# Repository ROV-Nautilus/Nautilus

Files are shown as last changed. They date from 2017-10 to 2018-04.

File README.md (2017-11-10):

# Nautilus
Les fonds marins réunissent aujourd'hui de nombreux secteurs et enjeux, tant professionels que particuliers. On y retrouve entre autre l'exploration sous-marine, la surveillance et maintenance d'installations professionelles, ainsi que la cartographie des fonds marins. Tout ces domaines demandent le développement de solutions techniques plus rentables et pratiques qu'une intervention humaine. Notre projet propose ainsi un ROV (Remotely Operated Vehicle) polyvalent et simple d'utilisation à cet effet.

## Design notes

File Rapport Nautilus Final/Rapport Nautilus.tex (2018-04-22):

\documentclass[a4paper,11pt]{report}
 
% Import des extensions
\usepackage[T1]{fontenc}
\usepackage[utf8]{inputenc}
\usepackage[francais]{babel}
\usepackage{graphicx}
\usepackage{color}
\usepackage[table]{xcolor}
\usepackage{colortbl}
\usepackage{geometry}
\usepackage{caption}
\usepackage{subcaption}
\usepackage{hyperref}
\usepackage{fullpage}
\usepackage{listings}
\usepackage{lipsum}
\usepackage{eso-pic}
\usepackage[nottoc]{tocbibind}
\geometry{hmargin=2.5cm,vmargin=3.5cm}

\definecolor{darkWhite}{rgb}{0.94,0.94,0.94}

\lstset{
  aboveskip=3mm,
  belowskip=-2mm,
  backgroundcolor=\color{darkWhite},
  basicstyle=\footnotesize,
  breakatwhitespace=false,
  breaklines=true,
  captionpos=b,
  commentstyle=\color{red},
  deletekeywords={...},
  escapeinside={\%*}{*)},
  extendedchars=true,
  framexleftmargin=16pt,
  framextopmargin=3pt,
  framexbottommargin=6pt,
  frame=tb,
  keepspaces=true,
  keywordstyle=\color{purple},
  literate=
  {²}{{\textsuperscript{2}}}1
  {⁴}{{\textsuperscript{4}}}1
  {⁶}{{\textsuperscript{6}}}1
  {⁸}{{\textsuperscript{8}}}1
  {€}{{\euro{}}}1
  {é}{{\'e}}1
  {è}{{\`{e}}}1
  {ê}{{\^{e}}}1
  {ë}{{\¨{e}}}1
  {É}{{\'{E}}}1
  {Ê}{{\^{E}}}1
  {û}{{\^{u}}}1
  {ù}{{\`{u}}}1
  {â}{{\^{a}}}1
  {à}{{\`{a}}}1
  {á}{{\'{a}}}1
  {ã}{{\~{a}}}1
  {Á}{{\'{A}}}1
  {Â}{{\^{A}}}1
  {Ã}{{\~{A}}}1
  {ç}{{\c{c}}}1
  {Ç}{{\c{C}}}1
  {õ}{{\~{o}}}1
  {ó}{{\'{o}}}1
  {ô}{{\^{o}}}1
  {Õ}{{\~{O}}}1
  {Ó}{{\'{O}}}1
  {Ô}{{\^{O}}}1
  {î}{{\^{i}}}1
  {Î}{{\^{I}}}1
  {í}{{\'{i}}}1
  {Í}{{\~{Í}}}1,
  morekeywords={*,...},
  numbers=left,
  numbersep=10pt,
  numberstyle=\tiny\color{black},
  rulecolor=\color{black},
  showspaces=false,
  showstringspaces=false,
  showtabs=false,
  stepnumber=1,
  stringstyle=\color{gray},
  tabsize=4,
  title=\lstname,
}

\newcommand{\blap}[1]{\vbox to 0pt{#1\vss}}
\newcommand\AtUpperLeftCorner[3]{%
\put(\LenToUnit{#1},\LenToUnit{\dimexpr\paperheight-#2}){\blap{#3}}%
}
\newcommand\AtTopCenterPage[2]{%
\put(\LenToUnit{.5\paperwidth},\LenToUnit{\dimexpr\paperheight-#1}){\blap{\hbox to 0pt{\hss#2\hss}}}%
}
\newcommand\AtUpperRightCorner[3]{%
\put(\LenToUnit{\dimexpr\paperwidth-#1},\LenToUnit{\dimexpr\paperheight-#2}){\blap{\llap{#3}}}%
}

\author{Dylan Bideau, Julien Turpin, Pierre Bogrand, Guillaume Vincenti}
\title{\huge{Nautilus - Rapport}}
\date{22 Avril 2018}

\begin{document}
\makeatletter
\begin{titlepage}

	\AddToShipoutPicture{
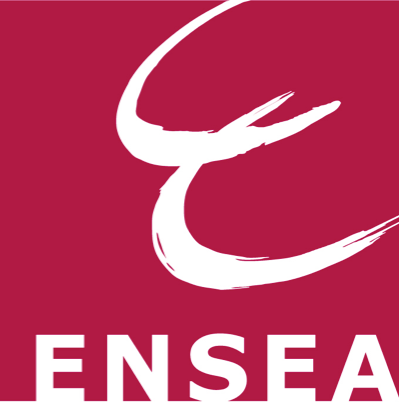
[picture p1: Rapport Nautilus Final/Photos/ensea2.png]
		\AtUpperLeftCorner{1.5cm}{1cm}{}
	}
	\AddToShipoutPicture{
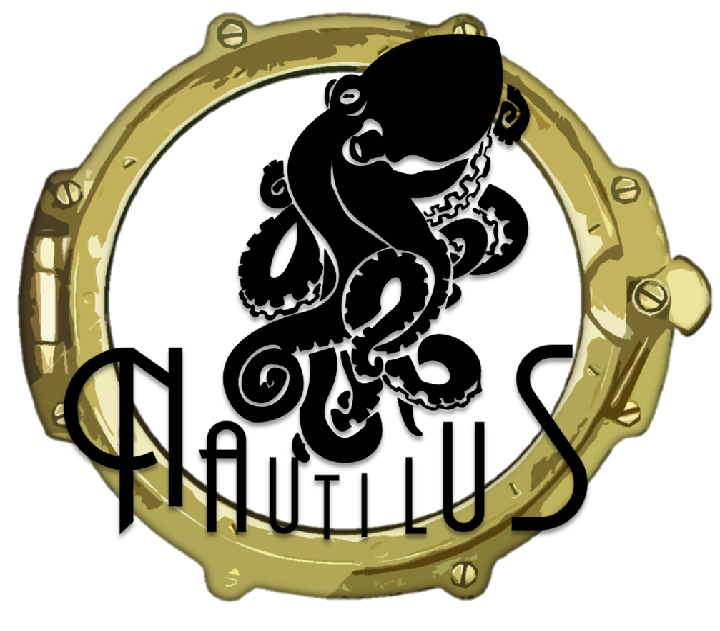
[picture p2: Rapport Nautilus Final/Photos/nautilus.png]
		\AtUpperRightCorner{1.5cm}{1cm}{}
	}

	\begin{center}
		\vspace*{10cm}
		\textsc{\@title}
		\vspace*{0.5cm}
		\hrule
		\vspace*{0.5cm}
		\large{\@author}
	\end{center}
	\vspace*{9.2cm}
	\begin{center}
		\large{\@date}
	\end{center}
\end{titlepage}
\ClearShipoutPicture

\renewcommand{\contentsname}{Sommaire}
\tableofcontents

\chapter{Introduction}

        Les fonds marins réunissent aujourd'hui de nombreux secteurs et enjeux, tant professionnels que particuliers. On y retrouve entre autre l'exploration sous-marine, la surveillance et maintenance d'installations professionnelles, ainsi que la cartographie des fonds marins. Tout ces domaines demandent le développement de solutions techniques plus rentables et pratiques qu'une intervention humaine. Notre projet propose ainsi un ROV (Remotely Operated Vehicle) polyvalent et simple d'utilisation à cet effet.

\chapter{Présentation du projet}
        
				Un ROV est un robot sous-marin contrôlé à distance et permettant une acquisition d'informations, visuelles ou à partir de capteurs. Notre projet de ROV filoguidé, Nautilus, sera transportable et pilotable à l'aide d'un ordinateur portable. Il permettra d'observer facilement des installations ou des fonds marins à l'aide de caméras. Disposant également de fonctions avancées, le Nautilus sera en mesure de recréer le fond marin d'une zone géographique déterminée par l'utilisateur à partir d'une batterie de photographies prises lors de la phase d'exploration. Les différentes fonctionnalités du Nautilus en font ainsi un outil polyvalent, permettant exploration, maintenance et cartographie des fonds.

\chapter{Cahier des charges}

        \section{Analyse Fonctionnelle}
						\subsection{Structure}
								Facilement transportable et peu encombrant.\newline
								\textbf{Contraintes :}
								\begin{itemize}
										\item Poids : 2-3kg
										\item Dimension : 300*200*150mm
										\item Étanche de norme IP 68 \newline \newline
									\end{itemize}

						\subsection{Commandabilité}
								Commandé à distance par une liaison filaire.\newline
								\textbf{Contraintes :}
								\begin{itemize}
										\item Câble : 15m
										\item Carte intégrée dans le ROV
										\item FPV (First Person View)
										\item Piloté au clavier\newline \newline
								\end{itemize}

						\subsection{Milieu d'utilisation}
								Adapté aux contraintes imposées par son environnement. \newline
								\textbf{Contraintes :}
								\begin{itemize}
										\item Eau non salé (moins de 1 g de sels dissous par kilogramme d'eau)
										\item Eau translucide (transmittance de la lumière entre 75\% et 95\%)
										\item Lieu : Piscine, lac
										\item Écoulement laminaire
										\item Courant marin inférieur à 2 nœuds
										\item Profondeur de 10m (résistant à 2 bars) \newline \newline
								\end{itemize}

						\subsection{Énergie}
								Être entièrement autonome. \newline
								\textbf{Contraintes :}
								\begin{itemize}
										\item Autonomie de 20 minutes
								\end{itemize}

						\subsection{Motorisation}
								Être mobile une fois immergé. \newline
								\textbf{Contraintes :}
								\begin{itemize}
										\item Propulsion électrique
										\item Déplacement horizontal (Vitesse maximale de 1m/s)
										\item Déplacement vertical (Vitesse maximale de 0.5m/s)
										\item Direction droite/gauche à 360 degrés   \newline \newline
								\end{itemize}

						\subsection{Acquisitions}
								Acquérir et transmettre l'information. \newline
								\textbf{Contraintes :}
								\begin{itemize}
										\item Acquisition et retransmission d'un signal vidéo
										\item Acquisition et stockage de photographies
										\item Mesure de la pression
										\item Mesure de la position relative avec signaux GPS
								\end{itemize}

\chapter{Outils de gestion}

        \section{Trello}
					Notre premier outil de gestion est Trello. Il nous permet de gérer notre projet en terme de planification des tâches. Nous utilisons un code couleur pour chaque membre du projet :
						\begin{figure}[!h]
							\begin{center}
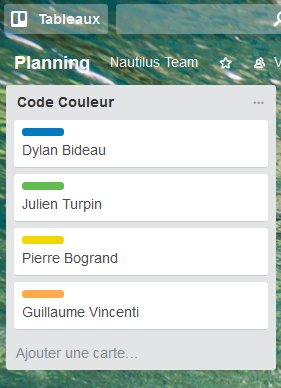
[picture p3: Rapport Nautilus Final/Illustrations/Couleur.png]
								
								\caption{Trello - Code Couleur}
							\end{center}
						\end{figure}
						\newline Voici actuellement ce que nous devons faire (Lors du premier livrable) :
						\begin{figure}[!h]
							\begin{center}
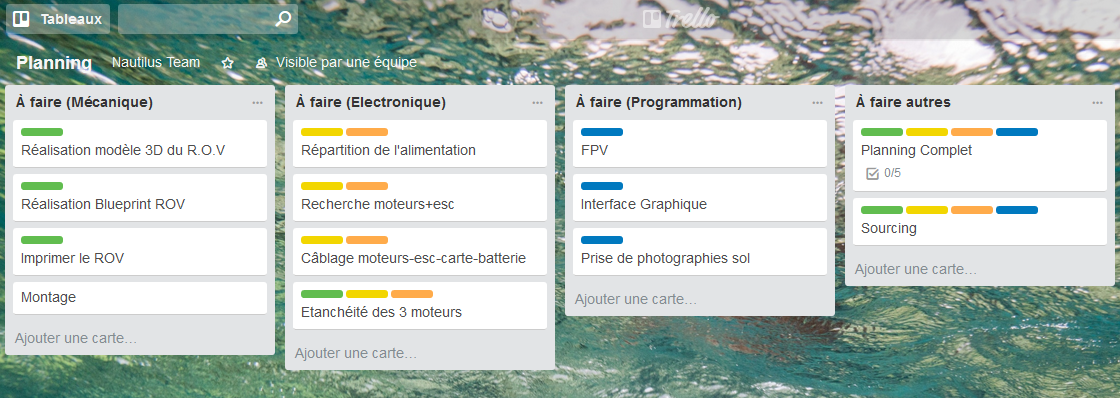
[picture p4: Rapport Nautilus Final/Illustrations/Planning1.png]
								
								\caption{Trello - Planning A faire}
							\end{center}
						\end{figure}
						\newpage Et ce que nous sommes en train de faire ainsi que les tâches terminées :
						\begin{figure}[!h]
							\begin{center}
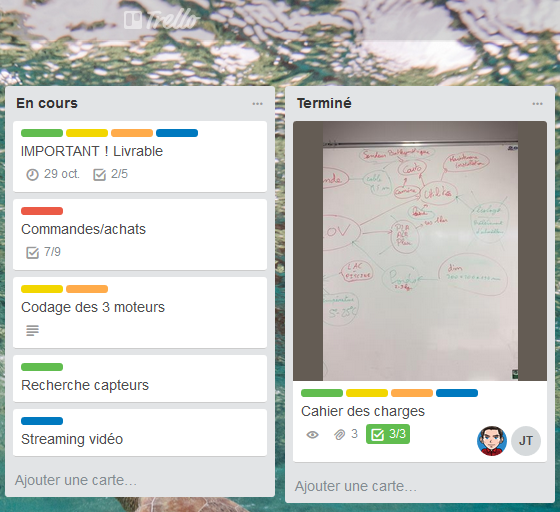
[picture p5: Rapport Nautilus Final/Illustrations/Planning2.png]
								
								\caption{Trello - Planning En cours et Terminé}
							\end{center}
						\end{figure}
						
        \section{Github}
				Tout notre code, que cela soit pour les documents en latex ou les codes liés au projet, est sur Github :
				\url{https://github.com/ROV-Nautilus/Nautilus}.
				\newline En voici un aperçu :
					\begin{figure}[!h]
							\begin{center}
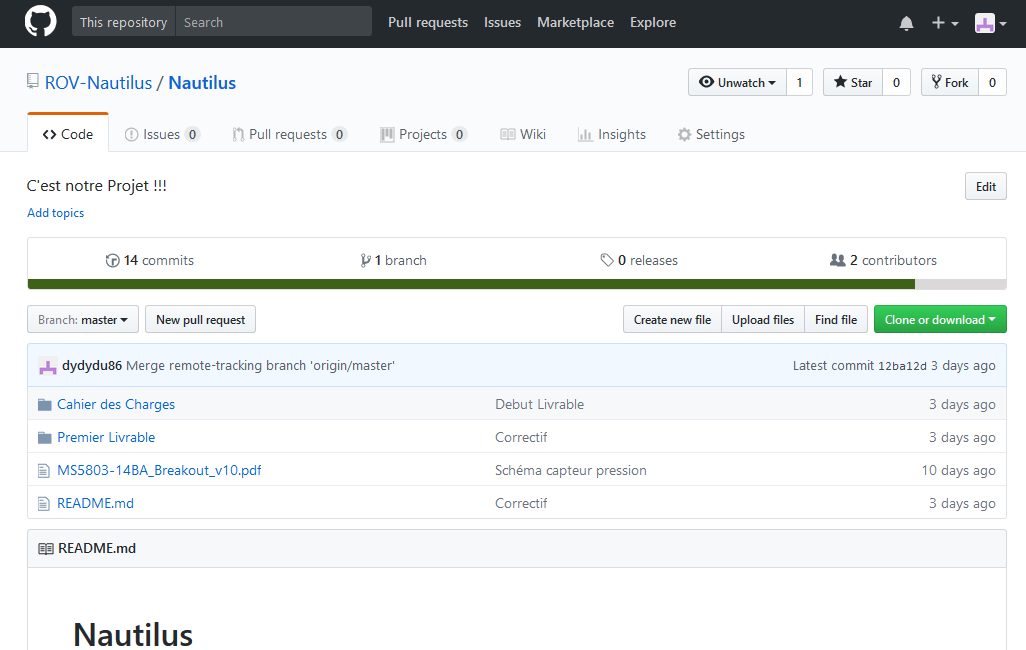
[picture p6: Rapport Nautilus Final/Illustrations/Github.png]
								
								\caption{Github - Nautilus}
							\end{center}
						\end{figure}
				
				\section{Gestion de Budget}
				La gestion de notre budget est réalisé à l'aide d'Excel et de Trello, en effet Trello nous permet de mettre en commun les propositions de dépenses et avec Excel nous stockons l'ensemble des commandes par fournisseurs. \newline \newline Les voici ci-dessous :
					\begin{figure}[!h]
							\begin{center}
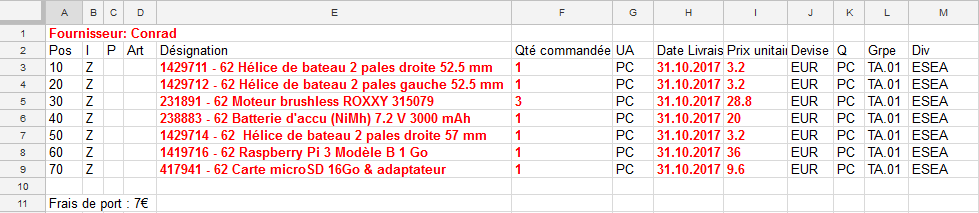
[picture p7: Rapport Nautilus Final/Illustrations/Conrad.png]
								
								\caption{Commande Conrad}
							\end{center}
					\end{figure}
					\begin{figure}[!h]
							\begin{center}
								
								\caption{Commande Robotshop}
							\end{center}
					\end{figure}
					\begin{figure}[!h]
							\begin{center}
								
								\caption{Commande ExpTech}
							\end{center}
					\end{figure}
								
\chapter{Motorisation et énergie}

				\section{Moteurs brushless et ESC} 
				
							Dans un premier temps, il a été question de la technologie des moteurs à utiliser. Après une étude des différentes solutions disponibles, nous avons finalement choisi des moteurs brushless \cite{ref5}. En effet, les moteurs brushless sont des machines synchrones auto-pilotées à aimants permanents et donc sans balais.
			\begin{figure}[!h]
				\begin{center}
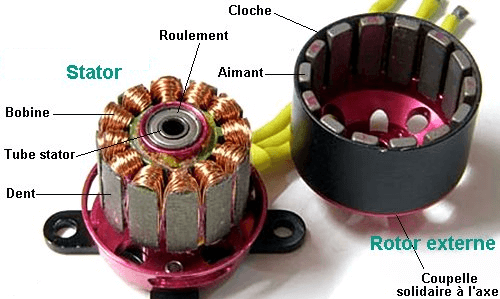
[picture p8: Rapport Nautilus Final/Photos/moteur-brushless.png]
					
					\caption{Moteur Brushless}
				\end{center}
			\end{figure}\newline
							Le principal avantage de ces moteurs est qu'ils peuvent être utilisés immergés dans l'eau sans aucun traitement particulier au préalable. En revanche, un système électronique de commande doit assurer la commutation du courant dans les enroulements statoriques : les ESC, ou Electronic Speed Controllers.
			Un ESC transforme un signal d'alimentation continu, dans notre cas issu d'une batterie, en un signal triphasé envoyé ensuite au moteur brushless. Pour contrôler la vitesse de rotation du moteur, on envoie à l'ESC un signal de commande, généralement créneau, et dont le rapport cyclique définit la vitesse du moteur. 
			\begin{figure}[!h]
				\begin{center}
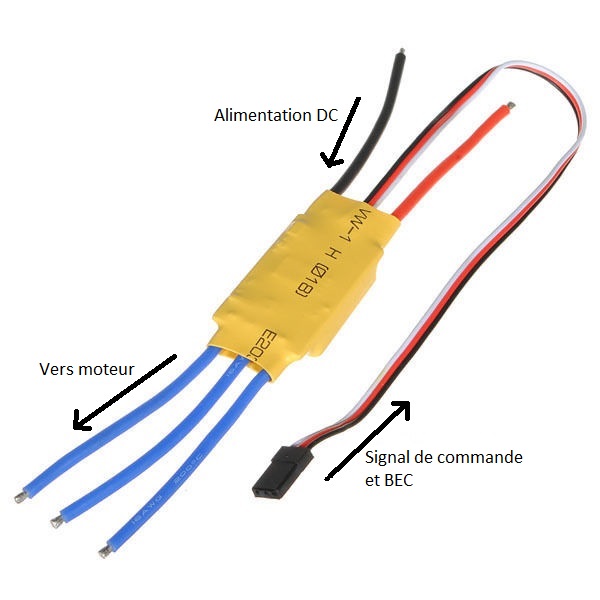
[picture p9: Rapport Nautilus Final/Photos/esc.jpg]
					
					\caption{ESC}
				\end{center}
			\end{figure}
			\newpage 
			Les trois ESC utilisés dans un premier temps pour nos moteurs \cite{ref6} sont également équipés d'un circuit éliminateur de batterie, ou BEC, permettant de générer un signal d'alimentation constant de 5V et 3A maximum. Ce dernier permet d'alimenter un autre composant, comme une carte Raspberry Pi dans notre cas, sans avoir à recourir à une seconde batterie. 
			\newline\newline Cependant, ces ESC ne permettent la rotation du moteur que dans un seul sens. Le seul moyen de modifier le sens de rotation du moteur dans ce cas est d'échanger deux des trois signaux déphasés envoyés au moteur. La direction droite/gauche étant assurée par les deux moteurs de propulsion arrière, cette particularité n'est pas problématique: la rotation plus rapide d'un des deux moteurs arrière par rapport à l'autre permet de diriger le ROV à gauche ou à droite. En revanche, le moteur vertical devant assuré la propulsion verticale doit pouvoir tourner dans les deux sens. Un second modèle d'ESC a donc été nécessaire pour permettre au moteur de tourner dans les deux sens. Ce dernier \cite{ref7} possède ainsi un mode "reverse" permettant au moteur de tourner dans les deux sens, ainsi qu'un BEC, et sera donc attribué au moteur vertical du ROV.
	
				\newpage\section{Calibration et commande des ESC}
				
				Traditionnellement, le signal de contrôle envoyé à l'ESC est un signal PWM de fréquence 50 Hz environ, un certain écart de cette valeur étant accepté. Dans notre cas, le signal est généré par une Raspberry Pi 3, et l'amplitude du signal est donc de 3,3 V environ.
				\begin{figure}[!h]
				  \begin{center}
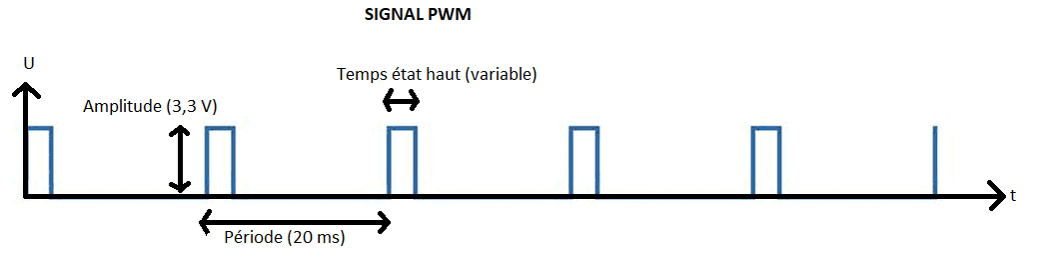
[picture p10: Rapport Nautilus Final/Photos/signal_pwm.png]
				  	
						\caption{Signal PWM}
				  \end{center}
		  	\end{figure}
				\newline\newline La caractéristique la plus importante de ce signal est la largeur de chaque impulsion. C'est cette dernière, généralement entre 0.5 ms et 2.5 ms, qui commande directement l'amplitude du signal envoyé aux moteurs et donc leur vitesse de rotation. Notre carte doit donc être capable de générer un signal créneau à 50 Hz, et de rapport cyclique variable sur commande. Pour générer un tel signal, on utilise le programme \cite{ref8}, disponible sur Github. En effet ce dernier a été conçu pour piloter des servomoteurs à partir des pins GPIO de la Raspberry Pi, et est donc le plus adapté pour générer un tel signal. Pour installer ServoBlaster sur la carte, on rentre les commandes suivantes sur le terminal de Raspbian:
				\begin{figure}[!h]
				  \begin{center}
				  	
						\caption{Programme Servoblaster}
				  \end{center}
		  	\end{figure}
				
				Une fois cette installation effectuée, on peut générer le signal à l'aide de la commande, toujours dans le terminal de Raspbian, "echo x=y > /dev/servoblaster", où x représente le GPIO que l'on utilise et y la valeur du temps d'état haut, en dizaine de us ( par exemple y=100 correspond à un temps d'état haut de 1 ms). Les valeurs de y peuvent aller de 50 à 250, correspondant respectivement à un temps haut de 0.5 ms et 2.5 ms. \newpage Les valeurs de x désignent les GPIO suivant:
					\begin{figure}[!h]
				  \begin{center}
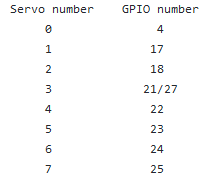
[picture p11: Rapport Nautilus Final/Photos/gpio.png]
				  	
						\caption{Valeurs GPIO}
				  \end{center}
		  	\end{figure}
				
				On obtient ainsi des commandes comme ci-dessous:
				
					\begin{figure}[!h]
				  \begin{center}
				  	
						\caption{Commandes moteurs}
				  \end{center}
		  	\end{figure}
			
			Avec chaque nouvelle valeur de y modifiant la valeur du temps haut du signal sortant. \newline
			
			Toutefois, avant leur utilisation, les ESC nécessitent d'être calibrés. En effet, en fonction des radiocommandes ou autre dispositifs de commande utilisés, l'intervalle des valeurs du temps d'état haut du signal de commande envoyé à l'ESC peux différer. L'ESC doit donc être calibré pour que la valeur maximale de temps d'état haut corresponde à la vitesse maximale de rotation du moteur. De même pour une valeur neutre (moteur à l'arrêt), et une valeur minimale correspondant à la vitesse de rotation inverse maximale, disponible uniquement pour l'ESC "Reverse"', et donc le moteur vertical associé. \newline
			La calibration ne peut pas être effectuée à l'aide des commandes issues de ServoBlaster, l'ESC nécessitant une variation douce du temps d'état haut pour cela. C'est le cas d'un joystick de télécommande, mais pas du programme ne permettant que des variations abrupts de la valeur du temps d'état haut. La calibration des ESC a donc été effectuée à l'aide d'une radiocommande disponible à l'ENSEA \cite{ref9}. Pour cela, on place le joystick de la manette au point neutre, on branche l'ESC à l'émetteur de la radiocommande et on allume dans l'ordre la radiocommande, puis l'ESC. Lorsque ce dernier s'allume, il associe ainsi automatiquement le signal en train d'être reçu au point neutre, donc moteur immobile. On effectue la même opération avec le joystick au maximum pour calibrer la valeur maximale de temps d'état haut et l'associer à la vitesse maximale de rotation du moteur. Une fois cette calibration effectuée, l'ESC en marche ne fonctionnera qu'après avoir reçu le signal correspondant à l'état neutre pendant un certain temps. Cela permet d'éviter entre autres un démarrage intempestif des moteurs. \newline
			
			Une fois la calibration effectuée, on observe à l'oscilloscope le signal de commande envoyé par la manette pour déterminer le temps d'état haut correspondant au point neutre, à la vitesse maximale, et à la vitesse maximale en rotation inverse pour le moteur vertical.
\newline On obtient les résultats suivants:
			
			\begin{figure}[!h]
				  \begin{center}
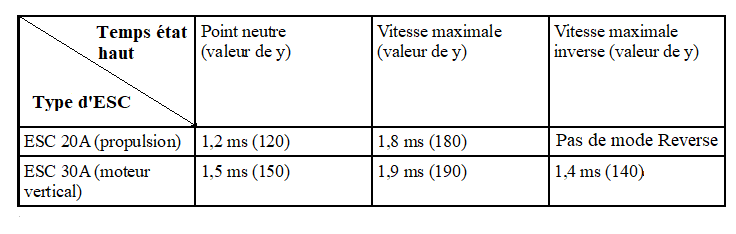
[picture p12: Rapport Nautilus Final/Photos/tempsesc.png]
				  	
						\caption{Tableau des temps}
				  \end{center}
		  	\end{figure}
				
				Après calibration et relevé de ces valeurs, on peut bien commander les 3 moteurs à l'aide des commandes de ServoBlaster. \newpage
				
				\section{Alimentation et montage}
				
				On utilise pour l'alimentation des ESC et des moteurs une batterie NiMh, de capacité 3000 mAh et délivrant une tension de 7,2 V \cite{ref10}. L'alimentation de la Raspberry est elle assurée par les BEC des ESC : ces derniers, mis en parallèle, délivrent une alimentation constante d'environ 5V et 3A, suffisante à alimenter la carte. On obtient donc le schéma fonctionnel suivant:
				\begin{figure}[!h]
				  \begin{center}
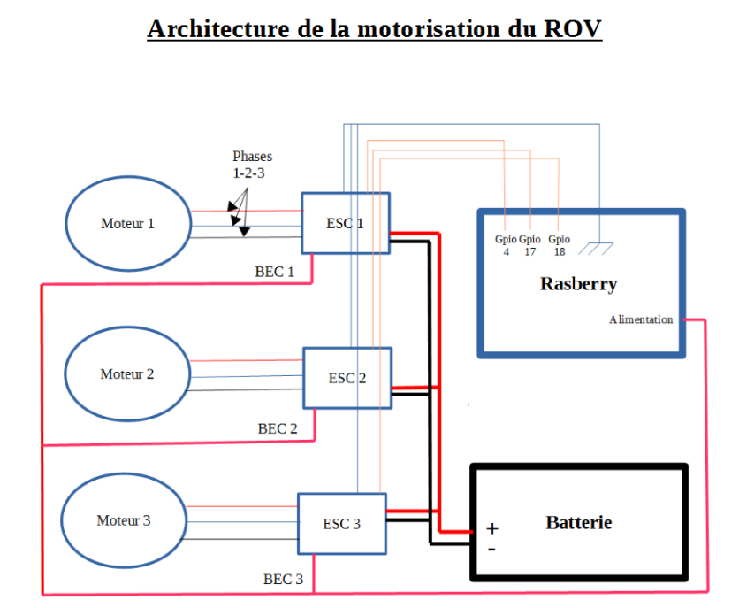
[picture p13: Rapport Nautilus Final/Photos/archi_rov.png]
				  	
						\caption{Architecture de la motorisation du ROV}
				  \end{center}
		  	\end{figure}

				Lorsque les 3 moteurs sont à leur vitesse maximale, avec la carte fonctionnelle, le courant prélevé sur la batterie est de 2A maximum. L'autonomie théorique dans cette configuration est donc d'environ 90 minutes. Toutefois cette dernière risque de diminuer avec l'utilisation et donc l'alimentation des différents capteurs, ainsi que la résistance de l'eau en condition.

\chapter{Acquisition et Commandabilité}
	
	Dans un second temps, nous devons relier les différents éléments de notre ROV sur une carte et ensuite traiter les informations reçues pour pouvoir agir sur les moteurs vus précédemment. Nous avons choisi la Raspberry.
	
	\section{Raspberry}
		Une partie de la programmation et des calculs est effectué sur une Raspberry PI 3 qui supportait tout les types de connections que l'on voulait, en voici la description.
			\begin{figure}[!h]
					\begin{center}
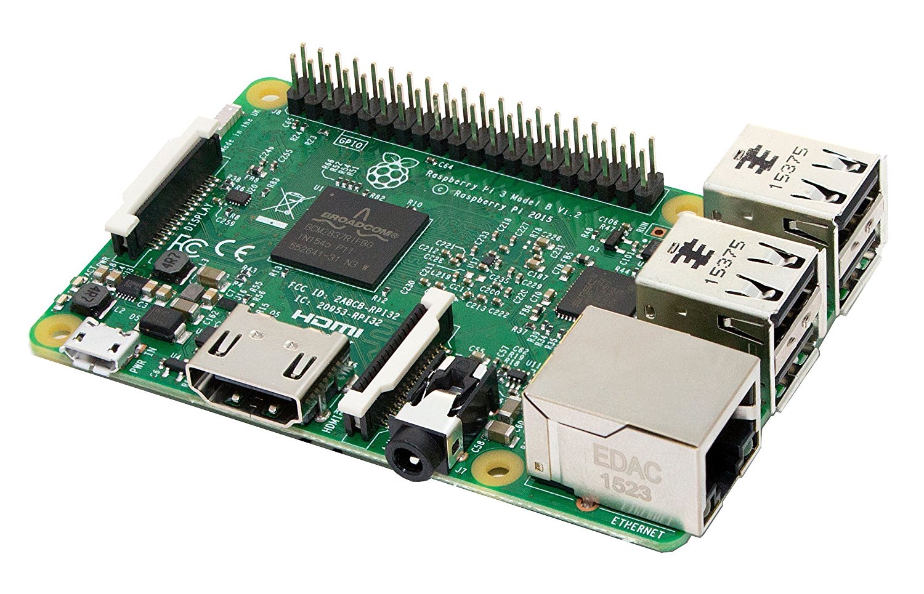
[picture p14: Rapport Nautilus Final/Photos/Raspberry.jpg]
						
						\caption{Raspberry}
					\end{center}
				\end{figure}
				
		\subsection{Cameras}
			Nous avons 2 caméras qui permettent, l'une la direction (vision frontale) et l'autre la cartographie (vision par dessous). Dans un premier temps, détaillons leur connexion entre la Raspberry et le traitement effectué par celle-ci.
			
				\subsubsection{Logitech C170}
					La première est une webcam Logitech C170, que nous avons démonté pour l'assemblage, relié en USB à la Raspberry. 
					\begin{figure}[!h]
					\begin{center}
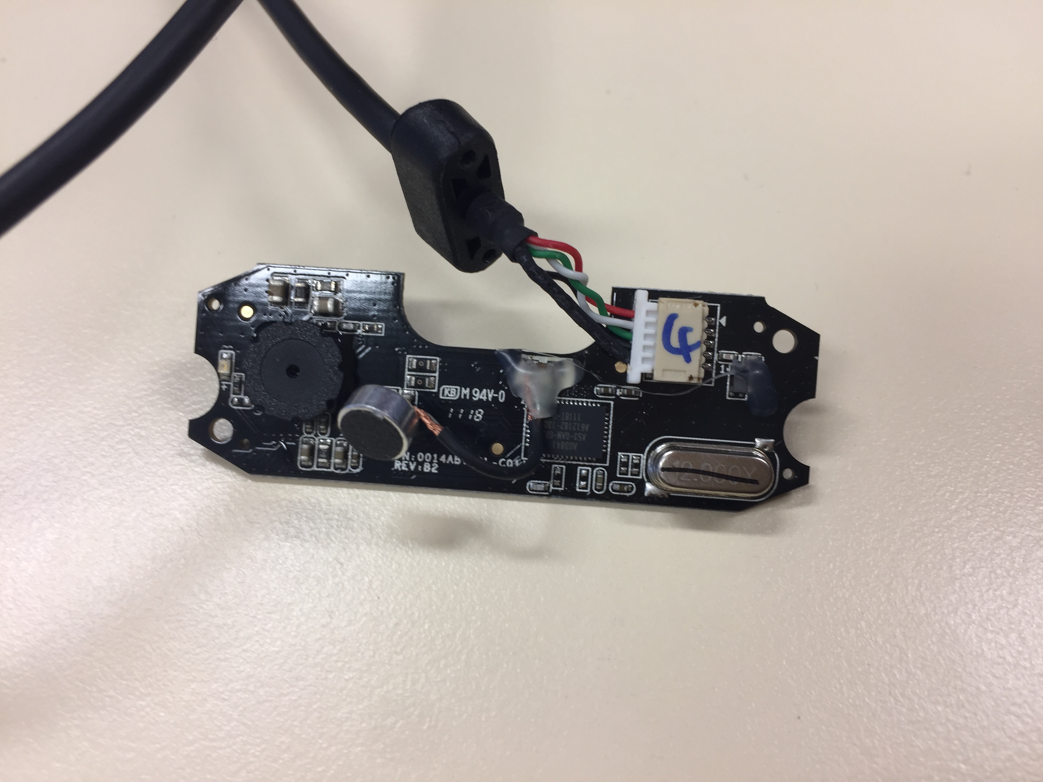
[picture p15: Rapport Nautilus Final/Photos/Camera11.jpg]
						
						\caption{Logitech C170}
					\end{center}
				\end{figure}
				\newline Nous l'avons choisi car le pilote de celle ci est deja installé nativement sur la Raspberry. Nous utilisons motion qui permet d'envoyer le flux vidéo venant de la camera et de le diffuser en ligne sur notre adresse local \cite{ref1}. En voici le résultat sur un navigateur:
				\begin{figure}[!h]
					\begin{center}
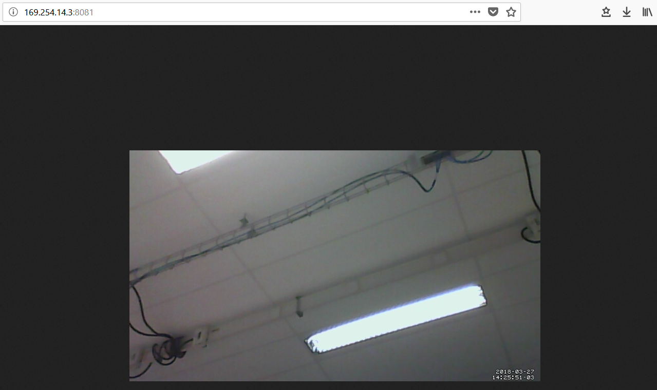
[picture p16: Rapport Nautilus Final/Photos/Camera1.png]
						
						\caption{Photo Caméra Frontale}
					\end{center}
				\end{figure}
				\newline Cette vidéo sera récupérée par l'interface (expliquée dans le chapitre associé) en 640*360.
				
				\subsubsection{Caméra V2}
					La deuxième est un module caméra pour Raspberry \cite{ref2} qui se raccorde directement par une nappe (un bus de type CSI-2). 
					\begin{figure}[!h]
					\begin{center}
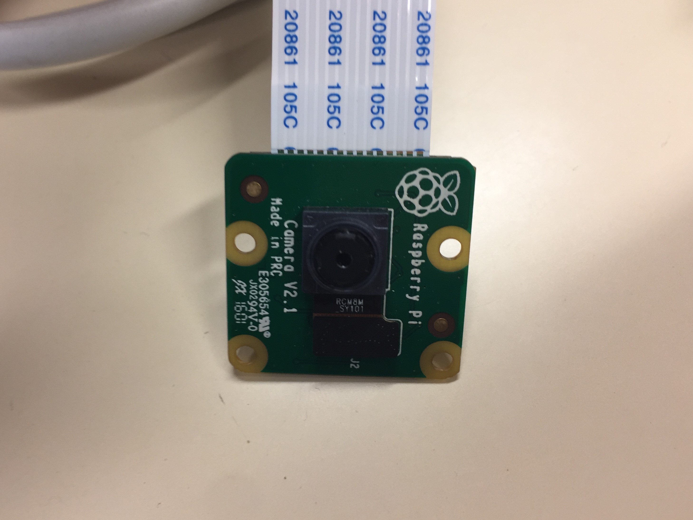
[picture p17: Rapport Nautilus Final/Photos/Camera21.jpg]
						
						\caption{Module Camera V2 Raspberry}
					\end{center}
				\end{figure}
				\newline Elle se paramètre en python avec les librairies données par le constructeur. De même que l'autre caméra, nous renvoyons un flux vidéo en ligne sur notre adresse local \cite{ref3} mais cette fois-ci sur un autre port.
				\newline
				\newline Le résultat sur un navigateur:
					\begin{figure}[!h]
					\begin{center}
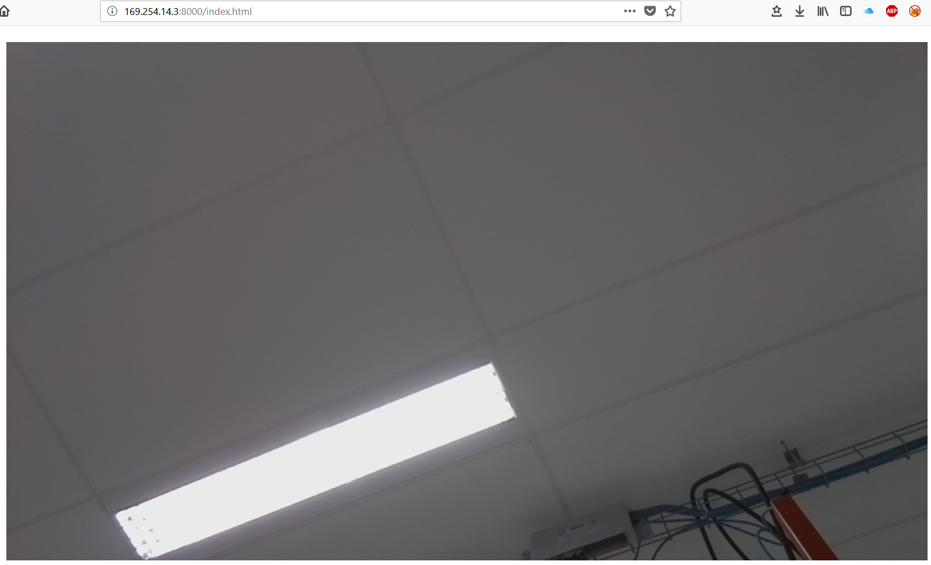
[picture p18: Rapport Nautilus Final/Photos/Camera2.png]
						
						\caption{Photo Caméra du dessous}
					\end{center}
				\end{figure}
				\newline La vidéo est diffusée en 1920*1080 et affichée par l'interface.
				\newpage
		
				\subsection{Capteur de Pression/Température}
		Le Nautilus est équipé d'un capteur lui permettent d'obtenir la température et la pression. Pour l'instant le ROV renvoit directement ces données mais il est envisageable d'utiliser par exemple la pression pour déterminer avec precision la profondeur du Nautilus. Le module utilisé pour notre ROV est le MS5803-14BA de Sparkfun \cite{ref11}.
		\newline
		
			\subsubsection{MS5803-14BA}
			\begin{figure}[!h]
					\begin{center}
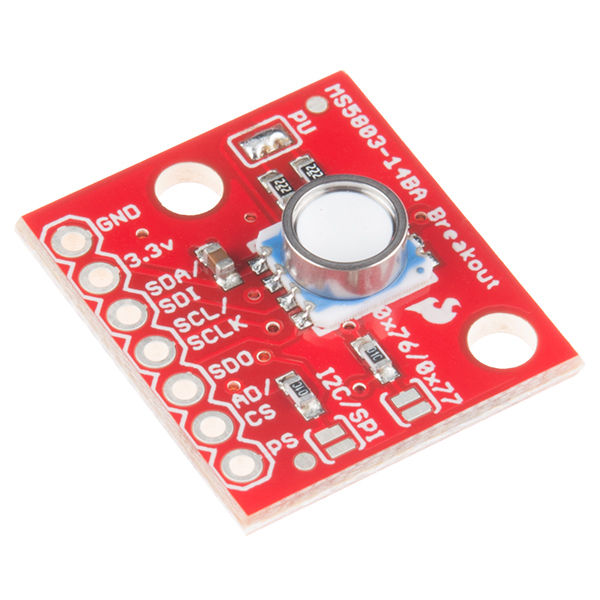
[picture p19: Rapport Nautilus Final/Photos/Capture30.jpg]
						
						\caption{Capteur de pression et de température MS5803-14BA}
					\end{center}
				\end{figure}
			Ce capteur de pression et de température dispose d'une membrane, pour des mesures de pressions de gaz ou de liquides, résistant à une pression de 30 Bar. De plus, il possède aussi des interfaces SPI et I2C. Nous utiliserons l'interface I2C car celle-ci utilise moins de connections et la fréquence de communication est basse. De plus bien que les deux modes de communication permettent de placer plusieurs modules sur un même câble, le SPI semble être limité sur la Raspberry. Dans nos conditions de connexion l'adresse esclave est 0x1E. Pour utiliser ce capteur on utilise directement un script python qui sera lancé à chaque fois que l'on veut obtenir la pression. Le script est disponible sur ce site \cite{ref12}.
			Comme ce capteur doit se trouver dans l'eau, nous l'avons recouvert, à l’exception de la membrane de résine Epoxy. \newline
			
				\begin{figure}[!h]
					\begin{center}
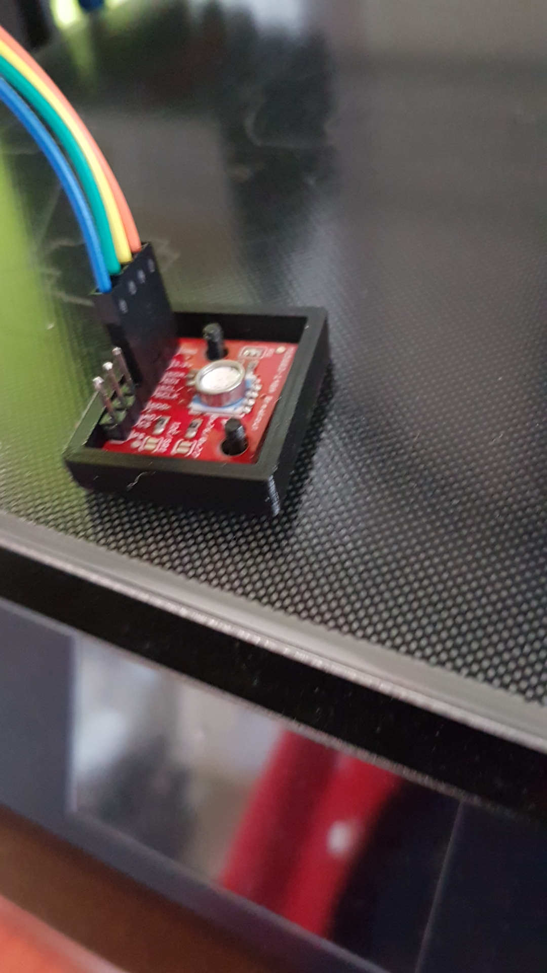
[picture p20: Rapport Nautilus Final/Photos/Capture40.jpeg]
						
						\caption{Capteur MS5803-14BA avant le coulage dans la résine}
					\end{center}
				\end{figure}
			\newpage
					
		\subsection{Centrale Inertielle}
		
		Le Nautilus dispose aussi d'une centrale inertielle. Avec celle-ci, le ROV peut déterminer son assiette ainsi que sa vitesse. Il est bien-sûr possible d'extrapoler ces données pour obtenir la position et suivre le déplacement du drone. Le module utilisé pour notre ROV est le MinIMU-9 v2 de Pololu \cite{ref13}.
		
			\subsubsection{MinIMU-9 v2}
			\begin{figure}[!h]
					\begin{center}
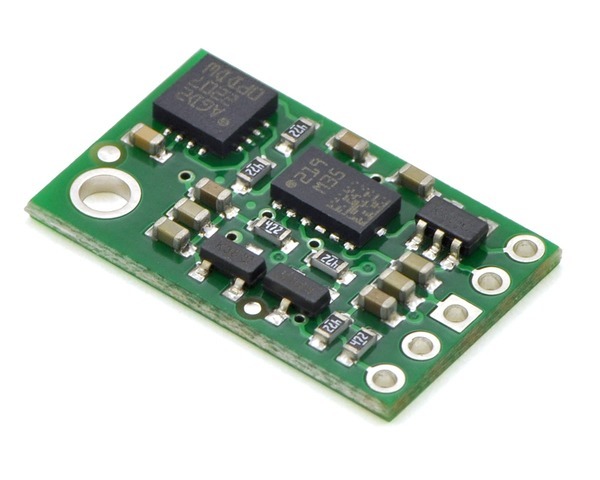
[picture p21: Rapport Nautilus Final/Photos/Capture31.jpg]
						
						\caption{Matrice inertielle MinIMU-9 v2}
					\end{center}
				\end{figure}
				Cette matrice inertielle se compose d'un gyroscope, d'un accéléromètre et d'un compas. De même ce module dispose des interfaces I2C et SPI mais nous utiliserons une fois encore le I2C. La complexité de la mise en place de cette matrice nous a poussé à aussi utiliser un code trouvé sur internet. Le script est disponible sur ce site \cite{ref14}. Ce code est accompagné d'un tutoriel permettant de mieux le comprendre et le mettre en place. Le code reconnait la matrice inertielle utilisée et donc s'adapte en connaissance, pas besoin de connaître l'adresse esclave. Nous avons quand même réalisé quelques modifications pour obtenir plus facilement les données en continue. En effet nous avons dans un premier temps modifier le fichier "`minimu9-ahrs.cpp"'. Celui-ci ne faisait qu'afficher les valeurs d'angles d’Euler dans le terminal. De plus la vitesse de retour des données était trop rapide, ces même donnée n'étaient pas stockées, et le système ne retournait pas uniquement les angles d’Euler. C'est pour cela que nous avons décidé de stocker les valeurs d'angles d’Euler dans un fichier texte qui se réinitialise toutes les 100 valeurs.
				\newline On remplace alors la ligne d'affichage 63-64 :
				\begin{lstlisting}[language=c++]
void output_euler(quaternion & rotation)
{
  std::cout << (vector)(rotation.toRotationMatrix().eulerAngles(2, 1, 0)
                        * (180 / M_PI));
}
				\end{lstlisting}
				Par le code suivant:
				\begin{lstlisting}[language=c++]

void output_euler(quaternion & rotation)
{
	if (c==100)
	{
		
		std::ofstream fichier("euler.txt", std::ios::out | std::ios::trunc);
		c=0;
		
		if(fichier)
		{
				
			fichier << ((vector)(rotation.toRotationMatrix().eulerAngles(2, 1, 0) * (180 / M_PI)))[0] <<'/'<<((vector)(rotation.toRotationMatrix().eulerAngles(2, 1, 0) * (180 / M_PI)))[1]<<'/'<<((vector)(rotation.toRotationMatrix().eulerAngles(2, 1, 0) * (180 / M_PI)))[2] << std::endl;
			c++;
			fichier.close();
		}
		else
		{
			std::cerr << "Impossible d'ouvrir le fichier !" << std::endl;
		}
	}
	else
	{
		std::ofstream fichier("euler.txt", std::ios::out | std::ios::app);
	
		if(fichier)
			{
				
				fichier << ((vector)(rotation.toRotationMatrix().eulerAngles(2, 1, 0) * (180 / M_PI)))[0] <<'/'<<((vector)(rotation.toRotationMatrix().eulerAngles(2, 1, 0) * (180 / M_PI)))[1]<<'/'<<((vector)(rotation.toRotationMatrix().eulerAngles(2, 1, 0) * (180 / M_PI)))[2] << std::endl;
				c++;
				fichier.close();
			}
			else
			{
				std::cerr << "Impossible d'ouvrir le fichier !" << std::endl;
			}
	}
	std::cout << c;
  
}}
				\end{lstlisting}
				
		On écrit une ligne 'std::cout << c;' pour voir si le compteur de valeurs présent dans le fichier text s'incrémente bien.  
		\newpage

	\section{PC}
		Maintenant que nous avons relié tous nos moteurs, caméras et capteurs à la Raspberry ainsi qu'un premier traitement des informations, nous allons voir comment nous traitons cela sur le PC.
		
		\subsection{Interface}
			En premier lieu parlons de l'interface, celle ci à pris différentes formes au cours du temps, ici nous présenterons que la dernière version. Toute la partie PC a été programmé en JAVA \cite{ref4}, l'interface utilise la bibliothèque graphique Swing qui nous permet de gérer l'affichage facilement que ce soit pour la vidéo ou pour les interactions.
			Lorsque l'application est lancée, nous arrivons donc dans un premier menu:
			\begin{figure}[!h]
					\begin{center}
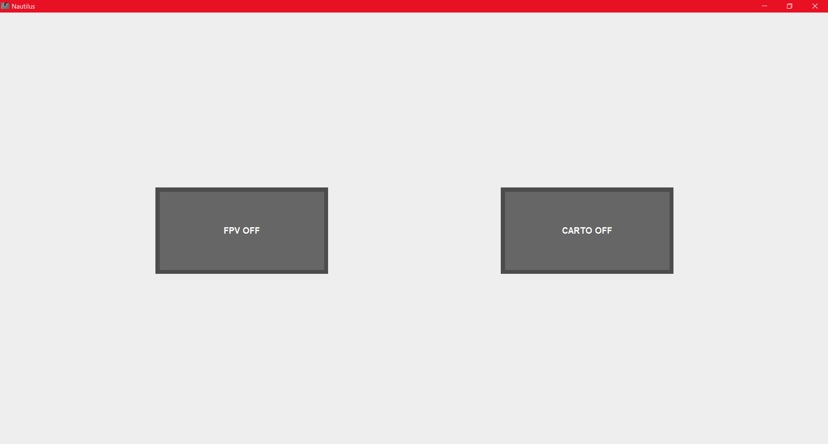
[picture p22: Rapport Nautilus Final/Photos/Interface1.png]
						
						\caption{Premier Menu Interface}
					\end{center}
				\end{figure}
				\newline Le bouton de Droite mène à une partie que nous développerons dans la partie~\ref{subsec:Cartographie} liée à la Cartographie.
				\newline \newline Nous avons donc crée une fenêtre JFrame:
				\begin{lstlisting}[language=java]
Interface inter = new Interface("Nautilus",0,0,1920,1080,true);
				\end{lstlisting}
				Elle est paramétrée de façon à prendre tous l'écran, ici 1920*1080, les objets se trouvant dans cette fenêtre sont gérés pour se placer en fonction de la taille de l’écran.
				\newline Le manager s'appelle GridBagLayout, il nécessite de paramétrer chaque objet.
				Ce manager crée une grille qui se construit en fonction des paramètres de chaque objet qu'il contient.
				\newpage Prenons exemple du premier bouton FPV:
				\begin{lstlisting}[language=java]
axPanel1.setMinimumSize(new Dimension(400,210));
axPanel1.setMaximumSize(new Dimension(400,210));
axPanel1.setPreferredSize(new Dimension(400,210));
c.fill = GridBagConstraints.BOTH;
c.anchor = GridBagConstraints.CENTER;
c.gridx = 0;
c.gridy = 0;
c.weighty = 0.0;
c.weightx = 0.0;
c.gridwidth = 1;
c.gridheight = 1;
c.insets = new Insets(0, 0, 0, 200);
				\end{lstlisting}
				Les 3 premières lignes correspondent à la taille du bouton, que nous avons choisi ici de garder fixe.
				\newline La ligne 4 n'est pas utile dans ce cas mais permet de correctement redimensionner l'objet lorsque la fenêtre change de taille.
				\newline La ligne 5 fixe l'objet au centre de la partie qui lui a été alloué.
				\newline La ligne 6 et 7 donne la ligne et la colonne où doit se situer l'objet.
				\newline La ligne 8 et 9 définissent des poids en x et y qui sont utilisé lors d'un redimensionnement, cela permet de donner plus de poids à un objet plutôt qu'à un autre. Nous ne l'utilisons pas d'où la valeur 0.
				\newline La ligne 10 et 11 permettent de définir combien de ligne et combien de colonne va prendre notre objet.
				\newline La ligne 12 insère une marge dans l'ordre suivant (margeSupérieure, margeGauche, margeInférieur, margeDroite).
				\newline Chaque objet de notre interface est défini de cette façon.
				\newline Ensuite il y a le bouton de Gauche qui lance le système complet. Un nouveau menu remplace le précédent:
				\begin{figure}[!h]
					\begin{center}
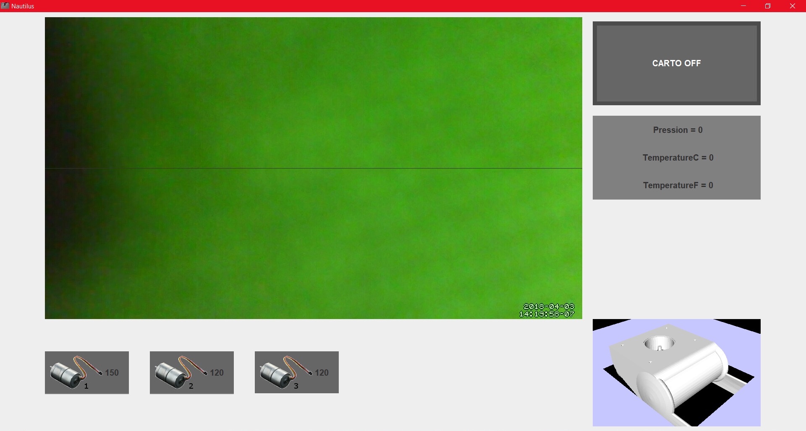
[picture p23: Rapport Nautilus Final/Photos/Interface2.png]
						
						\caption{Photo Deuxième menu interface}
					\end{center}
				\end{figure}
				\newline Nous avons maintenant la FPV en haut à gauche, le bouton à droite est le même précédemment, les informations des capteurs sont affichées à droite, les commandes envoyées aux moteurs sont en bas et pour finir un affichage 3D (\ref{subsec:Affichage 3D}) avec JAVA3D en bas à droite. Toutes les informations étant actualisées en temps réel avec la Raspberry. Nous allons voir comment.
				
		\subsection{Tunnel SSH}
			Nous avons choisi d'échanger les données avec la Raspberry par SSH, pour cela on utilise la bibliothèque Jcraft, plus précisément jsch. Au lancement de l'application, il y a 5 tunnels qui se créent (1 pour chaque caméras, 1 pour chaque capteurs et 1 pour les moteurs), ils sont crées au tout début pour ensuite permettre de transmettre directement les données sans refaire la procédure de connexion, le système gagne en rapidité. 
			\newline Détaillons maintenant la procédure qui permet de crée ses tunnels. Comme nous sommes en JAVA, une seule classe permet de crée un tunnel et cette classe est ensuite instanciée autant de fois que l'on veut.
			\newline Voici le code (Disponible dans /SSH/Exec.java) de création d'un tunnel :
			
			\begin{lstlisting}[language=java]
try{
	JSch jsch=new JSch();
	this.session=jsch.getSession("pi", "169.254.14.03", 22);
	UserInfo ui=new MyUserInfo();
  this.session.setUserInfo(ui);
  this.session.connect();
  this.channel = this.session.openChannel("exec");
  ((ChannelExec)this.channel).setCommand(this.Commande);
  this.channel.setInputStream(null);
  ((ChannelExec)this.channel).setErrStream(System.err);
  this.in=this.channel.getInputStream();
  this.channel.connect();
  byte[] tmp=new byte[1024];
  while(true){
		while(this.in.available()>0){
			int i=this.in.read(tmp, 0, 1024);
      if(i<0)break;
      System.out.print(new String(tmp, 0, i));
      this.retour=new String(tmp, 0, i);
    }
    if(channel.isClosed()){
			if(this.in.available()>0) continue; 
			System.out.println("exit-status: "+channel.getExitStatus());
      break;
     }
   }
}
catch(Exception e){
	System.out.println(e);
}
			\end{lstlisting}
			De la ligne 1 à 5, le tunnel est crée et les informations tel que le nom d'utilisateur, le mot de passe, l'adresse IP et le port sont ajouté aux couches correspondante du tunnel, puis ligne 6 la session est lancée.
		\newline A la ligne 7, nous ouvrons un canal d’exécution de commande et ligne 8 nous donnons à ce canal la commande que nous voulons envoyée.
		\newline Les lignes 9,10 et 11 définissent où vont les données entrées, sorties et sorties erreur. Dans notre cas l'entrée ne nous intéresse pas car cela passe par une commande, la sortie normal sera stockée et la sortie erreur renvoyée sur l'afficheur d'erreur du système (la console). La ligne 12 lance la connexion du canal, c'est ici que la commande est envoyée.
		\newline De la ligne 13 à 20 nous permet de récupérer les valeurs retournées par la Raspberry et de les stocker pour ensuite pouvoir les traiter.
		\newline Puis les dernières lignes, permettent de gérer le cas où le canal est coupé et nous renvoyer d'où vient l'erreur (par exceptions).
		\newline \newline Ces tunnels nous permettent d'envoyer des commandes à la Raspberry et de pouvoir récupérer le retour de cette commande. C'est par ce moyen que nous récupérons presque tous. L'exception étant pour la vidéo IP. Abordons ce sujet.
		\subsection{Vidéos}
		Nous avons donc 2 flux vidéos à récupérer depuis une adresse IP. Tout d'abord nous devons introduire quelque chose que nous utilisons partout dans notre code: le multi-Thread. Cela permet de lancer plusieurs actions en même temps, c'est ce qu'il se passe avec la récupération des flux vidéos. Chaque image des flux vidéos est récupérée, traitée puis affichée en temps réel sans interrompre le reste du programme, tout comme l'envoie de chaque commande.
		\newline Pour les flux vidéos, c'est une connexion http qui est effectuée, pour cela la méthode connect est appelée:
		\begin{lstlisting}[language=java]
public void connect()
	{
		try
		{
			URL u = new URL(useMJPGStream?mjpgURL:jpgURL);
			huc = (HttpURLConnection) u.openConnection();
			InputStream is = huc.getInputStream();
			connected = true;
			BufferedInputStream bis = new BufferedInputStream(is);
			dis= new DataInputStream(bis);
			if (!initCompleted) initDisplay();
		}
		catch(IOException e)
		{ //Relance la connexion si pas de connexion en attendant 60 sec
			try
			{
				huc.disconnect();
				Thread.sleep(60);
			}
			catch(InterruptedException ie)
			{
				System.out.println(ie);
			}
		}
		catch(Exception e){;}
	}
			\end{lstlisting}
			De la ligne 5 à 10, la procédure de connexion http est effectuée.
			\newline Après la ligne 12, on gère les exceptions liées à la connexion.
			\newline A la ligne 10, les données récupérées sont stockées dans une variable globale à Caméra.
			\newline Les informations vont être ensuite traité par initDisplay qui est appelée en ligne 11.
			\newline Observons cette méthode :
		\begin{lstlisting}[language=java]
public void initDisplay()
	{ 
		if (useMJPGStream)readMJPGStream();
		else
		{
			readJPG();
			disconnect();
		}
		imageSize = new Dimension((image.getWidth(this)*2), image.getHeight(this)*2);
		setPreferredSize(imageSize);
		parent.validate();
		initCompleted = true;
	}
		\end{lstlisting}
		Le premier If/Else permet de distinguer le cas où le flux serait une vidéo ou juste une photo. Dans notre cas c'est un flux vidéo composé d'image JPG.
		\newline Le reste de la méthode permet de préparer l'affichage des images.
		\newline Nous somme toujours dans la procédure de connexion, la lecture de la première image récupérée est faite. Pour cela la méthode readMJPGStream qui appel readJPG permet de décoder l'image et de la stocker dans la variable image. Voici les 2 méthodes :
		\begin{lstlisting}[language=java]
public void readMJPGStream()
	{
		readLine(4,dis); //enlève les 3 premières lignes
		readJPG();
		readLine(1,dis); //enlève les 2 dernières lignes
	}
	
public void readJPG()
	{
		try{
			JPEGImageDecoder decoder = JPEGCodec.createJPEGDecoder(dis);
			image = decoder.decodeAsBufferedImage();
		}catch(Exception e){
			disconnect();
		}
	}
		\end{lstlisting}
		La procédure de décodage d'une image JPEG est faite par une bibliothèque externe.
		\newpage Après cette procédure de connexion, les 2 méthodes ci dessus sont appelées en boucle et l'affichage mis à jour:
		\begin{lstlisting}[language=java]
public void readStream()
	{
		try{
			if (useMJPGStream){
				while(true){
					readMJPGStream();
					parent.repaint();
				}
			}
    	}catch(Exception e){;}
    }
		\end{lstlisting}
		L'affichage étant gérée par la bibliothèque Swing, c'est la méthode paint() qui affiche l'image et de plus trace une ligne qui en fonction des angles d’Euler renvoyés par la centrale inertielle :
		\begin{lstlisting}[language=java]
public void paint(Graphics g)
	{
		if (image != null)
			image=scale(image, 2);
			g.drawImage(image, 0, 0, this);
			Graphics2D g2 = (Graphics2D) g;
			double alpha = Interface.rotZ* Math.PI/180f;
    	int a = image.getHeight();
    	int b = image.getWidth();
    	double S =(b/2)*(Math.sin(alpha))*(Math.cos((Math.PI/2)-alpha));
    	double T =(b/2)*(Math.sin(alpha))*(Math.sin((Math.PI/2)-alpha));
    	g2.draw(new Line2D.Double(S,(a/2)-T,b-S,(a/2)+T));
	}
		\end{lstlisting}
	L'image est redimensionnée pour le bien de l'affichage et la ligne est tracé avec 2 points calculés par rapport à une rotation avec une origine au centre de l'image.
	\newline \newline Nos 2 flux vidéos sont donc récupérés et peuvent donc être appelés par un JPanel n'importe où.
\newpage
		\subsection{Capteurs et Moteurs}
		\subsubsection{Capteurs}
		Nous avons déjà précédemment préparé la Raspberry pour qu'elle renvoit les informations que l'on veut en fonction d'une commande. Il nous suffit maintenant d'envoyer en temps réel et en boucle infini les commandes (capteur de pression et centrale inertielle) grâce au système de multi-thread.
		\newline Expliquons la méthode pour le capteur de pression. Tout d'abord il faut crée le thread lié à la classe qui sera exécuté en boucle, puis on lance le thread avec la méthode, ce qui donne :
		\begin{lstlisting}[language=java]
Pression ex4 = new Pression();
Thread a4 = new Thread(ex4);
a4.start();
		\end{lstlisting}
		La classe Pression doit être héritière de Runnable pour permettre le lancement en thread.
		\newline Observons dans la classe Pression, la méthode start:
		\begin{lstlisting}[language=java]
Interface.exPression.Commander("python MS5803_14BA.py");
String[] a = Interface.exPression.retour.split("/");
this.Pression=a[0];
this.TemperatureC=a[1];
this.TemperatureF=a[2];
Interface.pre=Pression;
Interface.tempC=TemperatureC;
Interface.tempF=TemperatureF;
Interface.pression.setText(" Pression = "+Interface.pre);
Interface.pression.repaint();
Interface.temperatureC.setText(" TemperatureC = "+Interface.tempC);
Interface.temperatureC.repaint();
Interface.temperatureF.setText(" TemperatureF = "+Interface.tempF);
Interface.temperatureF.repaint();
		\end{lstlisting}
		Nous commençons en ligne 1 par envoyer la commande grâce au tunnel précédemment crée pour le capteur de Pression puis nous récupérons les valeurs sous forme de chaînes de caractères.
		\newline Enfin nous mettons à jour les valeurs globales et l’affichage.
		
		\subsubsection{Moteurs}
		Pour les moteurs, on envoie juste une commande à la Raspberry :
		\begin{lstlisting}[language=java]
Interface.exMoteur.setCommande("echo 0="+m1+" > /dev/servoblaster & echo 1="+m2+" > /dev/servoblaster & echo 2="+m3+" > /dev/servoblaster");
Thread a1 = new Thread(Interface.exMoteur);
a1.start();
while( a1.isAlive()) {}
Interface.m1=this.m1;
Interface.m2=this.m2;
Interface.m3=this.m3;
Interface.moteur1.setText(""+Interface.m1+"    ");
Interface.moteur1.repaint();
Interface.moteur2.setText(""+Interface.m2+"    ");
Interface.moteur2.repaint();
Interface.moteur3.setText(""+Interface.m3+"    ");
Interface.moteur3.repaint();
		\end{lstlisting}
		On oublie pas de mettre à jour au passage l'affichage.
		\newline Ce code est donc exécuté à chaque fois que l'on appuie sur une des touches de directions.
		\newline Nous avons défini les touches suivantes:
		\newline Monter/Descente : Z/S
		\newline Gauche/Droite : Flèche Gauche/Droite
		\newline Monter/Descente : Z/S
		\newline Arrête d'urgence : Barre Espace
		
		\subsection{Affichage 3D}
			\label{subsec:Affichage 3D}
			Nous utilisons JAVA3D pour afficher le modèle qui est extrait de Solidworks.
			\newline Tout d'abord nous devons crée un canvas 3D qui contiendra notre objet 3D et nous l’insérons au milieux d'un JPanel :
		\begin{lstlisting}[language=java]
Canvas3D canvas3D = new Canvas3D(SimpleUniverse.getPreferredConfiguration());
this.add(canvas3D, BorderLayout.CENTER);
		\end{lstlisting}
		Puis nous créons un simple univers qui contient notre canvas3D.
		\newline Nous devons maintenant positionner notre point d'observation pour avoir une vue correcte:
		\begin{lstlisting}[language=java]
OrbitBehavior orbit = new OrbitBehavior(canvas3D, OrbitBehavior.REVERSE_ROTATE);
orbit.setRotXFactor(0);//or any other value
orbit.setRotYFactor(0);
orbit.setTransXFactor(0);
orbit.setTransYFactor(0);
orbit.setSchedulingBounds(new BoundingSphere());
simpleU.getViewingPlatform().setViewPlatformBehavior(orbit);
ViewingPlatform vp = simpleU.getViewingPlatform();
TransformGroup steerTG = vp.getViewPlatformTransform();
Transform3D t3d = new Transform3D();
steerTG.getTransform(t3d);
t3d.lookAt(new Point3d(-1.2,1.2,1.2), new Point3d(0,0,0), new Vector3d(0,1,0));
t3d.invert();
steerTG.setTransform(t3d);
		\end{lstlisting}
		De la ligne 1 à 6, nous définissions un mouvement orbital de la caméra puis pour le moment nous fixons les rotations et les translations (on pourra les débloquer si on le veut)
		\newline Les lignes 9 à 14 permettent de définir la position initiale de notre point d'observation.
		\newline Nous devons ensuite crée ce qu'on appelle une scène, c'est dans cette scène que tous nos objets 3d se trouveront:
		\begin{lstlisting}[language=java]
BranchGroup scene = createSceneGraph(simpleU);
scene.compile();
simpleU.addBranchGraph(scene);
		\end{lstlisting}
		Les 2 ligns suivant compile la scène et rattache notre scène à l'univers.
		\newline \newline Maintenant nous devons crée cette scène 3d qui contiendra notre objet mais aussi la lumière, notre eau fictive et les mouvements possible.
		\newline Tous ce passe dans la méthode createSceneGraph.
		\begin{lstlisting}[language=java]
public BranchGroup createSceneGraph(SimpleUniverse simpleU) 
	{
    BranchGroup parent = new BranchGroup();
    BoundingSphere bounds = new BoundingSphere(new Point3d(), 100);
    Light ambientLight = new AmbientLight(new Color3f(Color.white));
    ambientLight.setInfluencingBounds(bounds);
    parent.addChild(ambientLight);
		
    Light directionalLight = new DirectionalLight(
      new Color3f(Color.white),
      new Vector3f(1, -1, -1));
    directionalLight.setInfluencingBounds(bounds);
    parent.addChild(directionalLight);
		\end{lstlisting}
		La ligne 3 crée un objet parent qui contiendra tous nos objets.
		\newline De la ligne à 4 à 7, on crée une lumière ambiante de couleur blanche
		\newline Puis de la ligne 9 à la ligne 13, une lumière directionnel pour augmenter la luminosité dans la même direction que notre point d'observation.
		\newline Nous ne détaillerons pas ici le code de la création de l'eau, le principe étant qu'on a crée 4 plans positionnés correctement autour du ROV et on lui applique une texture bleu (que l'on peut changer facilement). Et on oublie pas de l'ajouter à l'objet parent.
		\newline Maintenant autorisons les mouvements de la souris pour notre objet :
		\begin{lstlisting}[language=java]
TransformGroup mouseTransform = new TransformGroup();
mouseTransform.setCapability(TransformGroup.ALLOW_TRANSFORM_READ);
mouseTransform.setCapability(TransformGroup.ALLOW_TRANSFORM_WRITE);
mouseTransform.addChild(loadWavefrontObject());
		\end{lstlisting}
		Et en ligne 4 nous ajoutons notre ROV. La méthode loadWavefrontObject() permet de récupérer un objet 3D à partir d'un fichier .obj.
		\newline Pour la fin de cette méthode, les commentaires décrivent les opérations effectuées
		\begin{lstlisting}[language=java]
// Création de l'homethetie (homothetie)
Transform3D homothetie = new Transform3D();
homothetie.setScale(Interface.scale); 
    
// Création de la transformation (translation)
 Transform3D translation = new Transform3D();
translation.setTranslation(new Vector3f(0f, 0f, 0f));
translation.mul(homothetie);
    
// Création de la rotation X(rotation)
Transform3D rotationX = new Transform3D();
rotationX.rotX( Interface.rotX * Math.PI/180f);
rotationX.mul(translation);
    
// Création de la rotation Y(rotation)
Transform3D rotationY = new Transform3D();
rotationY.rotY( Interface.rotY * Math.PI/180f);
rotationY.mul(rotationX);
    
// Création de la rotation Z(rotation)
Transform3D rotationZ = new Transform3D();
rotationZ.rotZ( Interface.rotZ * Math.PI/180f);
rotationZ.mul(rotationY);
    
this.rotationGroup = new TransformGroup(rotationZ);

//Autorisation de modifier les transformations
rotationGroup.setCapability(TransformGroup.ALLOW_TRANSFORM_READ);
rotationGroup.setCapability(TransformGroup.ALLOW_TRANSFORM_WRITE);
    
// Ajout au graphe de la scène
rotationGroup.addChild(mouseTransform);
parent.addChild(rotationGroup);

return parent;
		\end{lstlisting}
		Notre scène renvoie donc tous les objets qu'on a crée précédemment.
		\newline \newline Maintenant nous voulons que notre ROV 3D soit capable de se mouvoir en fonction des angles d’Euler renvoyés et stockés dans notre interface.
		\newline Pour cela on a crée une méthode mouvement:
		\begin{lstlisting}[language=java]
public void mouvement(double rotX, double rotY, double rotZ, Vector3d trans, double scale)
		\end{lstlisting}
		Elle prend donc en argument, les 3 rotations, un vecteur des translations (sur tous les axes) et un paramètre multiplicateur d’échelle.
		\newline Cette méthode modifie la matrice 4*4 contenant la matrice de rotation, translation et de mise à l’échelle.
		\newline Puis effectue les transformations de cette matrice.
		
		\subsection{Cartographie}
			\label{subsec:Cartographie}
			Cette partie n'a pas été beaucoup développé mais un premier système a été crée mais pas intégré dans la dernière version de l'interface.
			\newline Grâce à l'appuie sur une touche, une photo de la camera du dessous est enregistrée dans un dossier. Voici le code qui permet d'enregistrer notre photo en jpg :
			\begin{lstlisting}[language=java]
BufferedImage img = new BufferedImage(axPanel.getWidth(), axPanel.getHeight(), BufferedImage.TYPE_INT_RGB);
axPanel.print(img.getGraphics());
try {
	ImageIO.write(img, "jpg", new File(nomPhoto+".jpg"));
}
catch (IOException e5) {
	e5.printStackTrace();
}
		\end{lstlisting}
			Le système n'est pas fini mais dans l'absolu chaque photo serai enregistrée avec un nom différent avec les données de localisation dans les méta-données de la photo.
			\newline Ensuite il y a un autre bouton (non affiché sur la dernière interface) qui ouvre une autre fenêtre avec toutes nos photos positionnées, en fonction des coordonnées GPS, sur une carte.
			\newline On peut cliquer sur chaque photo pour les agrandir dans une nouvelle fenêtre.
			\newline Tous les codes se trouvent dans le sous-dossier /Carto.
			
			\newpage	
			
\chapter{Structure}

	L'objectif suivant, et non des moindres dans la construction d'un véhicule sous-marin, était l'établissement de la structure. Comme on peut le voir dans le cahier des charges, la structure a été pensée dans 6 optiques différentes : étanchéité, transportabilité, durabilité, aqua-dynamisme, esthétisme et personnalisation. 
				
				\section{Design}
				
				Tout d'abord, il fallait donner un premier aspect à notre R.O.V. pour en suite le modifier après différents tests pour mieux correspondre aux 6 optiques explicitées au début. Pour obtenir des idées sur différentes architectures et aussi nous faire gagner du temps sur la conception du design, on a étudié plusieurs R.O.V. du marchés. Voici les 3 R.O.V qui ont eu la plus grosse influence sur notre design:
					
					\begin{figure}[!h]
						\centering
							\begin{subfigure}[b]{0.3\textwidth}
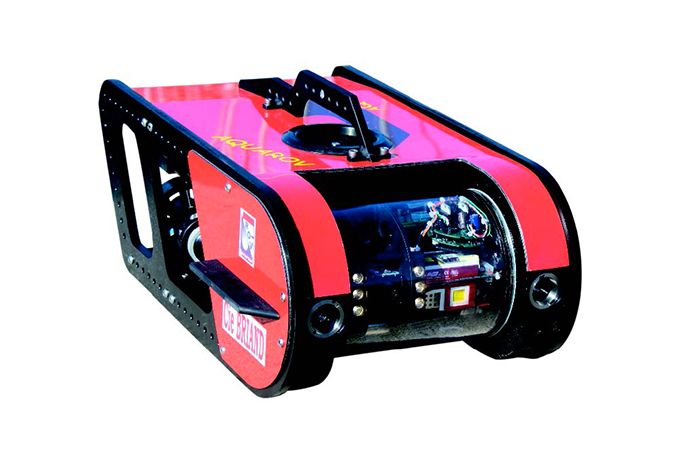
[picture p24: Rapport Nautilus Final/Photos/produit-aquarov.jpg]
								
								\caption{Aquarov de Rov developpement}
							\end{subfigure}
							\begin{subfigure}[b]{0.3\textwidth}
								
								\caption{SeaBotix d'Advanced Marine}
							\end{subfigure}
							\begin{subfigure}[b]{0.3\textwidth}
								
								\caption{Trident d'Open ROV}
							\end{subfigure}
					\end{figure}\newpage
					
					Avec le design de ces drones en tête, on a alors réalisé le notre qui se veut plus épuré dans la même lignée que le Trident. En effet cet aspect se destine mieux à un marché dit 'grand publique'. Très vite, après les premiers croquis, nous sommes passé à une conception sous SolidWorks du R.O.V.. Voici donc son aspect final sous Solidworks ainsi qu'un rendu 3D : 
					
					\begin{figure}[!h]
						\centering
							\begin{subfigure}[b]{0.5\textwidth}
								
							\end{subfigure}
							\begin{subfigure}[b]{0.5\textwidth}
								
							\end{subfigure}
							\caption{Modélisation du R.O.V. Nautilus sous Solidworks}
					\end{figure}
					
					\begin{figure}[!h]
						\centering
							\begin{subfigure}[b]{0.4\textwidth}
								
							\end{subfigure}
							\begin{subfigure}[b]{0.4\textwidth}
								
							\end{subfigure}
							\caption{rendu 3D du R.O.V. Nautilus sous Solidworks}
					\end{figure}
					
					Comme on peut l'observer le R.O.V. va se composer de 3 grandes parties : un squelette interne, un tube transparent ainsi qu'une coque. Cela va faciliter l'étanchéification du R.O.V mais aussi la modification ou le remplacement d'une partie sans toucher aux autres. On colle alors parfaitement aux sections esthétisme et personnalisation. Niveau dimensionnement,le R.O.V. a un encombrement total de 300*200*150 mm. 
						\newline
						\newline
					
				\subsection{Squelette interne}
				
				\begin{figure}[!h]
					\begin{center}
						
						\caption{squelette interne}
					\end{center}
				\end{figure}
				
				Le squelette interne du R.O.V. joue, comme son nom l'indique, le rôle d'une structure de soutient et de rigidification du Nautilus. C'est donc la partie du R.O.V. la plus résistante à la déformation. L'ensemble des autres parties, comme la coque,les câbles, ainsi que les trois moteurs brushless viennent se fixer dessus bénéficient ainsi de cette solidité. De plus comme l'eau va circuler énormément dans cette zone, le squelette interne a été conçu pour opposer très peu de résistance au passage de l'eau avec de nombreux trous et même concentrer et diriger les flux aux niveaux des moteurs. \newpage

				\subsection{Tube}	
				
				\begin{figure}[!h]
					\begin{center}
						
						\caption{Tube}
					\end{center}
				\end{figure}
				
			Le tube est la partie étanche du Nautilus. En effet, ce tube regroupera l'ensemble de l'électronique. Celui-ci est entièrement transparant pour d'une part permettre de filmer ainsi que de photographier à l'aide de nos deux caméras et d'autre part de permettre à l'utilisateur un contrôle visuel de l'électronique et de l'étanchéité.  
			
				\subsection{Coque}	
				
				\begin{figure}[!h]
					\begin{center}
						
						\caption{Coque}
					\end{center}
				\end{figure}
				
			La coque, quand à elle, va apporter le profil nécessaire à un bon aqua-dynamisme ainsi qu'une protection à l'environnement. Elle est aussi au coeur de la problématique de personnalisation car en plus de pouvoir avoir une forme ou une couleur différente, elle peut aussi accueillir des modules supplémentaires par exemple sur les bras à l'avant de sa coque.
			
			\section{Matériaux, méthode de construction}
			
			Une fois le design établi, nous sommes passé à la réalisation. Pour un premier prototypage rapide, nous avons choisi l'impression 3D de type ' fused filament fabrication'. Ainsi la coque a été imprimée en PLA et le squelette en ABS, tout deux avec un support en PVA qui est un plastique qui se dissous dans l'eau.
			
					\begin{figure}[!h]
						\centering
							\begin{subfigure}[b]{0.3\textwidth}
								
							\end{subfigure}
							\begin{subfigure}[b]{0.3\textwidth}
								
							\end{subfigure}
							\caption{impressions 3D du Nautilus}
					\end{figure}
				\begin{figure}[!h]
						\centering
							\begin{subfigure}[b]{0.3\textwidth}
								
							\end{subfigure}
							\begin{subfigure}[b]{0.3\textwidth}
								
							\end{subfigure}
							\caption{impressions 3D du Nautilus}
					\end{figure}
					
					Cependant pour de prochaines impressions de la coque, il sera nécessaire de revoir le positionnement de celle-ci dans la zone d'impression. En effet, les efforts qui s'exercent sur la coque coïncident avec l'agencement des couches de plastique. Ceci explique l'apparition de fissure sur la coque.

					\newpage
				
		Le tube est réalisé à l'aide d'un tube en acrylique dont une extrémité est un bouchon en acrylique scellé à la résine Epoxy et l'autre est aussi un bouchon avec un joint torique qui permet d'ouvrir le tube.
		
					\begin{figure}[!h]
						\centering
							\begin{subfigure}[b]{0.3\textwidth}
								
							\end{subfigure}
							\begin{subfigure}[b]{0.3\textwidth}
								
							\end{subfigure}
							\caption{réalisation du tube}
					\end{figure}
					
		Pour que l'ensemble des câbles rentrent dans le tube, un petit accès a été réalisé puis scellé à la résine Epoxy.
		
							\begin{figure}[!h]
						\centering
							\begin{subfigure}[b]{0.3\textwidth}
								
							\end{subfigure}
							\begin{subfigure}[b]{0.3\textwidth}
								
							\end{subfigure}
							\caption{accès des câbles et coulage de la résine }
					\end{figure}
			
			\section{Simulations poids et aqua-dynamisme}
					Une fois la structure réalisée avec Solidworks, on a attribué les matériaux ou des densités, quand le matériau n'était pas disponible, aux différents composant.\newline
				Pour un déplacement correct dans l'eau sans modification de l'assiette il faut que le centre d'inertie (en prenant en compte la poussée d’Archimède) soit confondu avec les axes des moteurs. On a donc rajouté des poids en plomb sur le drone en modifiant leurs poids jusqu'à obtenir la position du centre d'inertie voulue : 
					\begin{figure}[!h]
						\centering
							\begin{subfigure}[b]{0.3\textwidth}
								
							\end{subfigure}
							\begin{subfigure}[b]{0.3\textwidth}
								
							\end{subfigure}
							\caption{répartition du poids}
					\end{figure}\newline
					
				Avec une assiette correcte, on peut s'intéresser à l'aqua-dynamisme du ROV. En effet à l'aide du module flow-simulation de Solidworks, on place le Nautilus dans un cube de fluide s'écoulant à 2m/s (la vitesse maximale du ROV) et on regarde le comportement de certaines lignes de courants :
									
					\begin{figure}[!h]
					
						\centering
							\begin{subfigure}[b]{0.3\textwidth}
								
							\end{subfigure}
							\begin{subfigure}[b]{0.3\textwidth}
								
							\end{subfigure}
							\caption{test d'aqua-dynamisme}
							
					\end{figure}

				Comme on peut le voir, le fluide qui rencontre l'avant du ROV suit la paroi en accélérant à une vitesse semblable tout autour du Nautilus. Cet écoulement est bien caractéristique d'une bonne pénétration du ROV dans le fluide.\newpage
				
				\section{Test en eau}
				
				\begin{figure}[!h]
					\begin{center}
						
						\caption{ROV entièrement monté}
					\end{center}
				\end{figure}
				Une fois la structure entièrement réalisée et testée en simulation, nous avons réalisé les tests en eau. Cependant durant ces tests, nous nous sommes aperçu que le ROV n'était pas parfaitement étanche. En effet au bout d'une dizaine de minutes nous avons pu observer de l'humidité dans le tube. Bien que le reste de la structure se comporte parfaitement bien il faut revoir l'étanchéité du ROV.
			
\chapter{Conclusion}

Le projet Nautilus est un projet que nous avons proposé, et pour lequel nous ne sommes partis de rien. De l'établissement du cahier des charges aux premiers tests en eau, nous avons dû, avec l'aide de notre professeur encadrant, trouver pour chaque aspect du développement les solutions techniques qui nous paraissaient optimales. Ce projet nous a permis de découvrir ou de compléter nos connaissances dans de nombreux domaines, tant software et code que mécanique, électrique ou encore en CAO. Malgré un aboutissement permettant la présentation d'un produit final, ce dernier n'a malheureusement pas pu être testé pour vérifier sa conformité au cahier des charges d'origine, à cause d'un problème purement mécanique d'étanchéité, et de défaut de conception d'un des moteurs. Toutefois, plusieurs pistes d'améliorations peuvent être apportées au ROV, comme entre autre une impression différente de la structure pour une plus grande solidité, une révision de l'étanchéité du tube central, une installation d'une pompe à vide, et un meilleur agencement des composants à l'intérieur de ce dernier. Autant de possibilités donnent au projet Nautilus un aspect de développement à plus long terme.
\newline\newline Nous tenons également à remercier notre professeur encadrant, M. Goutailler, et Éric, de l'atelier mécanique de l'ENSEA, pour leur aide précieuse tout au long de l'avancement de notre projet.

\bibliographystyle{unsrt} % Le style est mis entre accolades.

\bibliography{bibliographie} % mon fichier de base de données s'appelle bibli.bib

\listoffigures

\end{document}

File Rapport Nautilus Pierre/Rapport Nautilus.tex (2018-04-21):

\documentclass[a4paper,11pt]{report}
 
% Import des extensions
\usepackage[T1]{fontenc}
\usepackage[utf8]{inputenc}
\usepackage[francais]{babel}
\usepackage{graphicx}
\usepackage{color}
\usepackage{colortbl}
\usepackage{geometry}
\usepackage{hyperref}
\usepackage{fullpage}
\usepackage{eso-pic}
\geometry{hmargin=2.5cm,vmargin=3.5cm}

\newcommand{\blap}[1]{\vbox to 0pt{#1\vss}}
\newcommand\AtUpperLeftCorner[3]{%
\put(\LenToUnit{#1},\LenToUnit{\dimexpr\paperheight-#2}){\blap{#3}}%
}
\newcommand\AtTopCenterPage[2]{%
\put(\LenToUnit{.5\paperwidth},\LenToUnit{\dimexpr\paperheight-#1}){\blap{\hbox to 0pt{\hss#2\hss}}}%
}
\newcommand\AtUpperRightCorner[3]{%
\put(\LenToUnit{\dimexpr\paperwidth-#1},\LenToUnit{\dimexpr\paperheight-#2}){\blap{\llap{#3}}}%
}

\author{Dylan Bideau, Julien Turpin, Pierre Bogrand, Guillaume Vincenti}
\title{\huge{Nautilus - Rapport}}
\date{10 Avril 2018}

\begin{document}
\makeatletter
\begin{titlepage}

	\AddToShipoutPicture{
		\AtUpperLeftCorner{1.5cm}{1cm}{}
	}
	\AddToShipoutPicture{
		\AtUpperRightCorner{1.5cm}{1cm}{}
	}

	\begin{center}
		\vspace*{10cm}
		\textsc{\@title}
		\vspace*{0.5cm}
		\hrule
		\vspace*{0.5cm}
		\large{\@author}
	\end{center}
	\vspace*{9.2cm}
	\begin{center}
		\large{\@date}
	\end{center}
\end{titlepage}
\ClearShipoutPicture

\renewcommand{\contentsname}{Sommaire}
\tableofcontents

\chapter{Introduction}

        Les fonds marins réunissent aujourd'hui de nombreux secteurs et enjeux, tant professionels que particuliers. On y retrouve entre autre l'exploration sous-marine, la surveillance et maintenance d'installations professionelles, ainsi que la cartographie des fonds marins. Tout ces domaines demandent le développement de solutions techniques plus rentables et pratiques qu'une intervention humaine. Notre projet propose ainsi un ROV (Remotely Operated Vehicle) polyvalent et simple d'utilisation à cet effet.

\chapter{Présentation du projet}
        
				Un ROV est un robot sous-marin contrôlé à distance et permettant une acquisition d'informations, visuelles ou à partir de capteurs. Notre projet de ROV filoguidé, Nautilus, sera transportable et pilotable à l'aide d'un ordinateur portable. Il permettra d'observer facilement des installations ou des fonds marins à l'aide de caméras. Disposant également de fonctions avancées, le Nautilus sera en mesure de recréer le fond marin d'une zone géographique déterminée par l'utilisateur à partir d'une batterie de photographies prises lors de la phase d'exploration. Les différentes fonctionnalités du Nautilus en font ainsi un outil polyvalent, permettant exploration, maintenance et cartographie des fonds.

\chapter{Cahier des charges}

        \section{Analyse Fonctionnelle}
						\subsection{Structure}
								Facilement transportable et peu emcombrant.\newline
								\textbf{Contraintes :}
								\begin{itemize}
										\item Poids : 2-3kg
										\item Dimension : 300*200*150mm
										\item Etanche de norme IP 68 \newline \newline
									\end{itemize}

						\subsection{Commandabilité}
								Commandé à distance par une liaison filaire.\newline
								\textbf{Contraintes :}
								\begin{itemize}
										\item Câble : 15m
										\item Carte intégrée dans le ROV
										\item FPV (First Person View)
										\item Piloté au clavier\newline \newline
								\end{itemize}

						\subsection{Milieu d'utilisation}
								Adapté aux contraintes imposées par son environnement. \newline
								\textbf{Contraintes :}
								\begin{itemize}
										\item Eau non salé (moins de 1 g de sels dissous par kilogramme d'eau)
										\item Eau translucide (transmittance de la lumière entre 75\% et 95\%)
										\item Lieu : Piscine, lac
										\item Ecoulement laminaire
										\item Courant marin inferieur à 2 noeuds
										\item Profondeur de 10m (résistant à 2 bars) \newline \newline
								\end{itemize}

						\subsection{Energie}
								Etre entièrement autonome. \newline
								\textbf{Contraintes :}
								\begin{itemize}
										\item Autonomie de 20 minutes
								\end{itemize}

						\subsection{Motorisation}
								Etre mobile une fois immergé. \newline
								\textbf{Contraintes :}
								\begin{itemize}
										\item Propulsion electrique
										\item Déplacement horizontal (Vitesse maximale de 1m/s)
										\item Déplacement vertical (Vitesse maximale de 0.5m/s)
										\item Direction droite/gauche à 360 degres   \newline \newline
								\end{itemize}

						\subsection{Acquisitions}
								Acquérir et transmettre l'information. \newline
								\textbf{Contraintes :}
								\begin{itemize}
										\item Acquisition et retransmission d'un signal vidéo
										\item Acquisition et stockage de photographies
										\item Mesure de la pression
										\item Mesure de la position relative avec signaux GPS
								\end{itemize}
													
\chapter{Motorisation et énergie}

				\section{Moteurs brushless et ESC} 
				
							Dans un premier temps, il a été question de la technologie des moteurs à utiliser. Après une étude des différentes solutions disponibles, nous avons finalement choisi des moteurs brushless (\href{http://www.conrad.fr/ce/fr/product/231891/Moteur-davion-lectrique-brushless-ROXXY-315079?ref=searchDetail}{Référence 1}). En effet, les moteurs brushless sont des machines synchrones auto-pilotées à aimants permanents et donc sans balais. \newline
			\begin{figure}[!h]
				\begin{center}
					
				\end{center}
			\end{figure}\newline
							Le principal avantage de ces moteurs est qu'ils peuvent être utilisés immergés dans l'eau sans aucun traitement particulier au préalable. En revanche, un système électronique de commande doit assurer la commutation du courant dans les enroulements statoriques : les ESC, ou Electronic Speed Controllers.
			Un ESC transforme un signal d'alimentation continu, dans notre cas issu d'une batterie, en un signal triphasé envoyé ensuite au moteur brushless. Pour contrôler la vitesse de rotation du moteur, on envoie à l'ESC un signal de commande, généralement créneau, et dont le rapport cyclique définit la vitesse du moteur. 
			\begin{figure}[!h]
				\begin{center}
					
				\end{center}
			\end{figure}
			\newpage 
			Les trois ESC utilisés dans un premier temps pour nos moteurs (\href{https://www.robotshop.com/eu/fr/esc-multirotor-20a-m20a.html}{Référence 2}) sont également équipés d'un circuit éliminateur de batterie, ou BEC, permettant de générer un signal d'alimentation constant de 5V et 3A maximum. Ce dernier permet d'alimenter un autre composant, comme une carte Raspberry Pi dans notre cas, sans avoir à recourir à une seconde batterie. 
			\newline\newline Cependant, ces ESC ne permettent la rotation du moteur que dans un seul sens. Le seul moyen de modifier le sens de rotation du moteur dans ce cas est d'échanger deux des trois signaux déphasés envoyés au moteur. La direction droite/gauche étant assurée par les deux moteurs de propulsion arrière, cette particularité n'est pas problématique: la rotation plus rapide d'un des deux moteurs arrière par rapport à l'autre permet de diriger le ROV à gauche ou à droite. En revanche, le moteur verical devant assuré la propulsion verticale doit pouvoir tourner dans les deux sens. Un second modèle d'ESC a donc été nécessaire pour permettre au moteur de tourner dans les deux sens. Ce dernier (\href{https://hobbyking.com/fr_fr/hobbykingr-tm-brushless-car-esc-30a-w-reverse.html}{Référence 3}) possède ainsi un mode "reverse" permettant au moteur de tourner dans les deux sens, ainsi qu'un BEC, et sera donc attribué au moteur vertical du ROV.
	
				\newpage\section{Calibration et commande des ESC}
				
				Traditionnellement, le signal de contrôle envoyé à l'ESC est un signal PWM de fréquence 50 Hz environ, un certain écart de cette valeur étant accepté. Dans notre cas, le signal est généré par une Raspberry Pi 3, et l'amplitude du signal est donc de 3,3 V environ.
				\begin{figure}[!h]
				  \begin{center}
				  	
				  \end{center}
		  	\end{figure}
				\newline\newline La caractéristique la plus importante de ce signal est la largeur de chaque impulsion. C'est cette dernière, généralement entre 0.5 ms et 2.5 ms, qui commande directement l'amplitude du signal envoyé aux moteurs et donc leur vitesse de rotation. Notre carte doit donc être capable de générer un signal créneau à 50 Hz, et de rapport cyclique variable sur commande. Pour générer un tel signal, on utlise le programme \href{https://github.com/richardghirst/PiBits/tree/master/ServoBlaster}{ServoBlaster}, disponible sur Github. En effet ce dernier a été conçu pour piloter des servomoteurs à partir des pins GPIO de la Raspberry Pi, et est donc le plus adapté pour générer un tel signal. Pour installer ServoBlaster sur la carte, on rentre les commandes suivantes sur le terminal de Raspbian:
				\begin{figure}[!h]
				  \begin{center}
				  	
				  \end{center}
		  	\end{figure}
				
				Une fois cette installation effectuée, on peut générer le signal à l'aide de la commande, toujours dans le terminal de Raspbian, "echo x=y > /dev/servoblaster", où x représente le GPIO que l'on utilise et y la valeur du temps d'état haut, en dizaine de us ( par exemple y=100 correspond à un temps d'état haut de 1 ms). Les valeurs de y peuvent aller de 50 à 250, correspondant respectivement à un temps haut de 0.5 ms et 2.5 ms. \newpage Les valeurs de x désignent les GPIO suivant:
					\begin{figure}[!h]
				  \begin{center}
				  	
				  \end{center}
		  	\end{figure}
				
				On obtient ainsi des commandes comme ci-dessous:
				
					\begin{figure}[!h]
				  \begin{center}
				  	
				  \end{center}
		  	\end{figure}
			
			Avec chaque nouvelle valeur de y modifiant la valeur du temps haut du signal sortant. \newline
			
			Toutefois, avant leur utilisation, les ESC nécessitent d'être calibrés. En effet, en fonction des radiocommandes ou autre dispositifs de commande utilisés, l'intervalle des valeurs du temps d'état haut du signal de commande envoyé à l'ESC peux différer. L'ESC doit donc être calibré pour que la valeur maximale de temps d'état haut corresponde à la vitesse maximale de rotation du moteur. De même pour une valeur neutre (moteur à l'arrêt), et une valeur minimale correspondant à la vitesse de rotation inverse maximale, disponible uniquement pour l'ESC "Reverse"', et donc le moteur vertical associé. \newline
			La calibration ne peut pas être effectuée à l'aide des commandes issues de ServoBlaster, l'ESC nécessitant une variation douce du temps d'état haut pour cela. C'est le cas d'un joystick de télécommande, mais pas du programme ne permettant que des variations abrupts de la valeur du temps d'état haut. La calibration des ESC a donc été effectuée à l'aide d'une radiocommande disponible à l'ENSEA (\href{https://www.topmodel.fr/product-detail-18656-graupner-mx-20-hott-12160?lang=fr}{Référence 4}). Pour celà, on place le joystick de la manette au point neutre, on branche l'ESC à l'émetteur de la radiocommande et on allume dans l'ordre la radiocommande, puis l'ESC. Lorsque ce dernier s'allume, il associe ainsi automatiquement le signal en train d'être reçu au point neutre, donc moteur immobile. On effectue la même opération avec le joystick au maximum pour calibrer la valeur maximale de temps d'état haut et l'associer à la vitesse maximale de rotation du moteur. Une fois cette calibration effectuée, l'ESC en marche ne fonctionnera qu'après avoir reçu le signal correspondant à l'état neutre pendant un certain temps. Celà permet d'éviter entre autres un démarrage intempestif des moteurs. \newline
			
			Une fois la calibration effectuée, on observe à l'oscilloscope le signal de commande envoyé par la manette pour déterminer le temps d'état haut correspondant au point neutre, à la vitesse maximale, et à la vitesse maximale en rotation inverse pour le moteur vertical. \newpage On obtient les résultats suivants:
			
			\begin{figure}[!h]
				  \begin{center}
				  	
				  \end{center}
		  	\end{figure}
				
				Après calibration et relevé de ces valeurs, on peut bien commander les 3 moteurs à l'aide des commandes de ServoBlaster. \newpage
				
				\section{Alimentation et montage}
				
				On utilise pour l'alimentation des ESC et des moteurs une batterie NiMh, de capacité 3000 mAh et délivrant une tension de 7,2 V (\href{http://www.conrad.fr/ce/fr/product/206028/Batterie-daccumulateurs-NiMh-72-V-3000-mAh-Conrad-energy-206028-stick-fiche-Tamiya-mle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}{Référence 5}). L'alimentation de la Raspberry est elle assurée par les BEC des ESC : ces derniers, mis en parallèle, délivrent une alimentation constante d'environ 5V et 3A, suffisante à alimenter la carte. On obtient donc le schéma fonctionnel suivant:
				\begin{figure}[!h]
				  \begin{center}
				  	
				  \end{center}
		  	\end{figure}

				Lorsque les 3 moteurs sont à leur vitesse maximale, avec la carte fonctionnelle, le courant prélevé sur la batterie est de 2A maximum. L'autonomie théorique dans cette configuration est donc d'environ 90 minutes. Toutefois cette dernière risque de diminuer avec l'utilisation et donc l'alimentation des différents capteurs, ainsi que la résistance de l'eau en condition.
				
\chapter{Structure}

	L'objectif suivant, et non des moindres dans la contruction d'un véhicule sous-marin, était l'établissement de la structure. Comme on peut le voir dans le cahier des charges, la structure a été pensée dans 6 optiques différentes : étanchéité, transportabilité, durabilité, aqua-dynamisme, esthétisme et personnalisation. 
				
				\section{Design}
				
				Tout d'abord, il fallait donner un premier aspect à notre R.O.V. pour en suite le modifier après différents tests pour mieux correspondre aux 6 optiques explicitées au début. Pour obtenir des idées sur différentes architectures et aussi nous faire gagner du temps sur la conception du design, on a étudié plusieurs R.O.V. du marchés. Voici les 3 R.O.V qui ont eu la plus grosse influence sur notre design:
				\begin{figure}[!h]
				  \centering
						\
				  	
				  \end{center}
		  	\end{figure}

\chapter{Références}

				\textbf{Motorisation et énergie :}
				\begin{itemize}
							\item \textbf{\href{http://www.conrad.fr/ce/fr/product/231891/Moteur-davion-lectrique-brushless-ROXXY-315079?ref=searchDetail}{Référence 1}} : Moteur d'avion électrique brushless ROXXY 315079 chez Conrad (x3)
							\item \textbf{\href{https://www.robotshop.com/eu/fr/esc-multirotor-20a-m20a.html}{Référence 2}} : ESC Suppo Multirotor 20A M20A chez RobotShop (x3)
							\item \textbf{\href{https://hobbyking.com/fr_fr/hobbykingr-tm-brushless-car-esc-30a-w-reverse.html}{Référence 3}} : ESC HobbyKing 30A avec Reverse (x1)
							\item \textbf{\href{https://www.topmodel.fr/product-detail-18656-graupner-mx-20-hott-12160?lang=fr}{Référence 4}} : Radiocommande Graupner MX-20 (disponible à l'ENSEA)
							\item \textbf{\href{http://www.conrad.fr/ce/fr/product/206028/Batterie-daccumulateurs-NiMh-72-V-3000-mAh-Conrad-energy-206028-stick-fiche-Tamiya-mle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}{Référence 5}} : Batterie d'accumulateurs (NiMh) 7.2 V 3000 mAh Conrad (x1)
				\end{itemize}

\end{document}

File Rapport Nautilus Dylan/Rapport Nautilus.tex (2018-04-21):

\documentclass[a4paper,11pt]{report}
 
% Import des extensions
\usepackage[T1]{fontenc}
\usepackage[utf8]{inputenc}
\usepackage[francais]{babel}
\usepackage{graphicx}
\usepackage{color}
\usepackage[table]{xcolor}
\usepackage{colortbl}
\usepackage{geometry}
\usepackage{hyperref}
\usepackage{fullpage}
\usepackage{listings}
\usepackage{eso-pic}
\usepackage[nottoc]{tocbibind}
\geometry{hmargin=2.5cm,vmargin=3.5cm}

%\lstset{numbers=left, stepnumber =1, firstnumber =1, numberfirstline=true, frame=lines}

\definecolor{darkWhite}{rgb}{0.94,0.94,0.94}

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

\newcommand{\blap}[1]{\vbox to 0pt{#1\vss}}
\newcommand\AtUpperLeftCorner[3]{%
\put(\LenToUnit{#1},\LenToUnit{\dimexpr\paperheight-#2}){\blap{#3}}%
}
\newcommand\AtTopCenterPage[2]{%
\put(\LenToUnit{.5\paperwidth},\LenToUnit{\dimexpr\paperheight-#1}){\blap{\hbox to 0pt{\hss#2\hss}}}%
}
\newcommand\AtUpperRightCorner[3]{%
\put(\LenToUnit{\dimexpr\paperwidth-#1},\LenToUnit{\dimexpr\paperheight-#2}){\blap{\llap{#3}}}%
}

\author{Dylan Bideau, Julien Turpin, Pierre Bogrand, Guillaume Vincenti}
\title{\huge{Nautilus - Rapport}}
\date{10 Avril 2018}

\begin{document}
\makeatletter
\begin{titlepage}

	\AddToShipoutPicture{
		\AtUpperLeftCorner{1.5cm}{1cm}{}
	}
	\begin{center}
		\vspace*{10cm}
		\textsc{\@title}
		\vspace*{0.5cm}
		\hrule
		\vspace*{0.5cm}
		\large{\@author}
	\end{center}
	\vspace*{9.2cm}
	\begin{center}
		\large{\@date}
	\end{center}
\end{titlepage}
\ClearShipoutPicture

\renewcommand{\contentsname}{Sommaire}
\tableofcontents

\chapter{Introduction}

        Les fonds marins réunissent aujourd'hui de nombreux secteurs et enjeux, tant professionnels que particuliers. On y retrouve entre autre l'exploration sous-marine, la surveillance et maintenance d'installations professionnelles, ainsi que la cartographie des fonds marins. Tout ces domaines demandent le développement de solutions techniques plus rentables et pratiques qu'une intervention humaine. Notre projet propose ainsi un ROV (Remotely Operated Vehicle) polyvalent et simple d'utilisation à cet effet.

\chapter{Présentation du projet}
        
				Un ROV est un robot sous-marin contrôlé à distance et permettant une acquisition d'informations, visuelles ou à partir de capteurs. Notre projet de ROV filoguidé, Nautilus, sera transportable et pilotable à l'aide d'un ordinateur portable. Il permettra d'observer facilement des installations ou des fonds marins à l'aide de caméras. Disposant également de fonctions avancées, le Nautilus sera en mesure de recréer le fond marin d'une zone géographique déterminée par l'utilisateur à partir d'une batterie de photographies prises lors de la phase d'exploration. Les différentes fonctionnalités du Nautilus en font ainsi un outil polyvalent, permettant exploration, maintenance et cartographie des fonds.

\chapter{Cahier des charges}

        \section{Analyse Fonctionnelle}
						\subsection{Structure}
								Facilement transportable et peu encombrant.\newline
								\textbf{Contraintes :}
								\begin{itemize}
										\item Poids : 2-3kg
										\item Dimension : 300*200*150mm
										\item Étanche de norme IP 68 \newline \newline
									\end{itemize}

						\subsection{Commandabilité}
								Commandé à distance par une liaison filaire.\newline
								\textbf{Contraintes :}
								\begin{itemize}
										\item Câble : 15m
										\item Carte intégrée dans le ROV
										\item FPV (First Person View)
										\item Piloté au clavier\newline \newline
								\end{itemize}

						\subsection{Milieu d'utilisation}
								Adapté aux contraintes imposées par son environnement. \newline
								\textbf{Contraintes :}
								\begin{itemize}
										\item Eau non salé (moins de 1 g de sels dissous par kilogramme d'eau)
										\item Eau translucide (transmittance de la lumière entre 75\% et 95\%)
										\item Lieu : Piscine, lac
										\item Écoulement laminaire
										\item Courant marin inférieur à 2 nœuds
										\item Profondeur de 10m (résistant à 2 bars) \newline \newline
								\end{itemize}

						\subsection{Énergie}
								Être entièrement autonome. \newline
								\textbf{Contraintes :}
								\begin{itemize}
										\item Autonomie de 20 minutes
								\end{itemize}

						\subsection{Motorisation}
								Être mobile une fois immergé. \newline
								\textbf{Contraintes :}
								\begin{itemize}
										\item Propulsion électrique
										\item Déplacement horizontal (Vitesse maximale de 1m/s)
										\item Déplacement vertical (Vitesse maximale de 0.5m/s)
										\item Direction droite/gauche à 360 degrés   \newline \newline
								\end{itemize}

						\subsection{Acquisitions}
								Acquérir et transmettre l'information. \newline
								\textbf{Contraintes :}
								\begin{itemize}
										\item Acquisition et retransmission d'un signal vidéo
										\item Acquisition et stockage de photographies
										\item Mesure de la pression
										\item Mesure de la position relative avec signaux GPS
								\end{itemize}
								
\chapter{Acquisition et Commandabilité}
	
	Dans un second temps, nous devons relier les différents éléments de notre ROV sur une carte et ensuite traiter les informations reçu pour pouvoir agir sur les moteurs vus précédemment. Nous avons choisi la Raspberry.
	
	\section{Raspberry}
		Une partie de la programmation et des calculs est effectué sur une Raspberry PI 3 qui supportait tout les types de connections que l'on voulait, en voici la description.
			\begin{figure}[!h]
					\begin{center}
						
						\caption{Raspberry}
					\end{center}
				\end{figure}
				
		\subsection{Cameras}
			Nous avons 2 caméras qui permettent, l'une la direction (vision frontale) et l'autre la cartographie (vision par dessous). Dans un premier temps, détaillons leur connexion entre la Raspberry et le traitement effectué par celle-ci.
			
				\subsubsection{Logitech C170}
					La première est une webcam Logitech C170, que nous avons démonté pour l'assemblage, relié en USB à la Raspberry. 
					\begin{figure}[!h]
					\begin{center}
						
						\caption{Logitech C170}
					\end{center}
				\end{figure}
				\newline Nous l'avons choisi car le pilote de celle ci est deja installé nativement sur la Raspberry. Nous utilisons motion qui permet d'envoyer le flux vidéo venant de la camera et de le diffuser en ligne sur notre adresse local \cite{ref1}. En voici le résultat sur un navigateur:
				\begin{figure}[!h]
					\begin{center}
						
						\caption{Photo Caméra Frontale}
					\end{center}
				\end{figure}
				\newline Cette vidéo sera récupérée par l'interface (expliquée dans le chapitre associé) en 640*360.
				
				\subsubsection{Caméra V2}
					La deuxième est un module caméra pour Raspberry \cite{ref2} qui se raccorde directement par une nappe (un bus de type CSI-2). 
					\begin{figure}[!h]
					\begin{center}
						
						\caption{Module Camera V2 Raspberry}
					\end{center}
				\end{figure}
				\newline Elle se paramètre en python avec les librairies données par le constructeur. De même que l'autre caméra, nous renvoyons un flux vidéo en ligne sur notre adresse local \cite{ref3} mais cette fois-ci sur un autre port.
				\newline
				\newline Le résultat sur un navigateur:
					\begin{figure}[!h]
					\begin{center}
						
						\caption{Photo Caméra du dessous}
					\end{center}
				\end{figure}
				\newline La vidéo est diffusée en 1920*1080 et affichée par l'interface.
				
		\subsection{Capteur de Pression/Température}
		
		\subsection{Central Inertielle}
		Julien
		\newpage
	\section{PC}
		Maintenant que nous avons relié tous nos moteurs, caméras et capteurs à la Raspberry ainsi qu'un premier traitement des informations, nous allons voir comment nous traitons cela sur le PC.
		
		\subsection{Interface}
			En premier lieu parlons de l'interface, celle ci à pris différentes formes au cours du temps, ici nous présenterons que la dernière version. Toute la partie PC a été programmé en JAVA \cite{ref4}, l'interface utilise la bibliothèque graphique Swing qui nous permet de gérer l'affichage facilement que ce soit pour la vidéo ou pour les interactions.
			Lorsque l'application est lancée, nous arrivons donc dans un premier menu:
			\begin{figure}[!h]
					\begin{center}
						
						\caption{Premier Menu Interface}
					\end{center}
				\end{figure}
				\newline Le bouton de Droite mène à une partie que nous développerons dans la partie~\ref{subsec:Cartographie} liée à la Cartographie.
				\newline \newline Nous avons donc crée une fenêtre JFrame:
				\begin{lstlisting}[language=java]
Interface inter = new Interface("Nautilus",0,0,1920,1080,true);
				\end{lstlisting}
				Elle est paramétrée de façon à prendre tous l'écran, ici 1920*1080, les objets se trouvant dans cette fenêtre sont gérés pour se placer en fonction de la taille de l’écran.
				\newline Le manager s'appelle GridBagLayout, il nécessite de paramétrer chaque objet.
				Ce manager crée une grille qui se construit en fonction des paramètres de chaque objet qu'il contient.
				\newpage Prenons exemple du premier bouton FPV:
				\begin{lstlisting}[language=java]
axPanel1.setMinimumSize(new Dimension(400,210));
axPanel1.setMaximumSize(new Dimension(400,210));
axPanel1.setPreferredSize(new Dimension(400,210));
c.fill = GridBagConstraints.BOTH;
c.anchor = GridBagConstraints.CENTER;
c.gridx = 0;
c.gridy = 0;
c.weighty = 0.0;
c.weightx = 0.0;
c.gridwidth = 1;
c.gridheight = 1;
c.insets = new Insets(0, 0, 0, 200);
				\end{lstlisting}
				Les 3 premières lignes correspondent à la taille du bouton, que nous avons choisi ici de garder fixe.
				\newline La ligne 4 n'est pas utile dans ce cas mais permet de correctement redimensionner l'objet lorsque la fenêtre change de taille.
				\newline La ligne 5 fixe l'objet au centre de la partie qui lui a été alloué.
				\newline La ligne 6 et 7 donne la ligne et la colonne où doit se situer l'objet.
				\newline La ligne 8 et 9 définissent des poids en x et y qui sont utilisé lors d'un redimensionnement, cela permet de donner plus de poids à un objet plutôt qu'à un autre. Nous ne l'utilisons pas d'où la valeur 0.
				\newline La ligne 10 et 11 permettent de définir combien de ligne et combien de colonne va prendre notre objet.
				\newline La ligne 12 insére une marge dans l'ordre suivant (margeSupérieure, margeGauche, margeInférieur, margeDroite).
				\newline Chaque objet de notre interface est défini de cette façon.
				\newline Ensuite il y a le bouton de Gauche qui lance le système complet. Un nouveau menu remplace le précédent:
				\begin{figure}[!h]
					\begin{center}
						
						\caption{Photo Deuxième menu interface}
					\end{center}
				\end{figure}
				\newline Nous avons maintenant la FPV en haut à gauche, le bouton à droite est le même précédemment, les informations des capteurs sont affichées à droite, les commandes envoyées aux moteurs sont en bas et pour finir un affichage 3D (\ref{subsec:Affichage 3D}) avec JAVA3D en bas à droite. Toutes les informations étant actualisées en temps reel avec la Raspberry. Nous allons voir comment.
				
		\subsection{Tunnel SSH}
			Nous avons choisi d'échanger les données avec la Raspberry par SSH, pour cela on utilise la bibliothèque Jcraft, plus précisément jsch. Au lancement de l'application, il y a 5 tunnels qui se créent (1 pour chaque caméras, 1 pour chaque capteurs et 1 pour les moteurs), ils sont crées au tout début pour ensuite permettre de transmettre directement les données sans refaire la procédure de connexion, le système gagne en rapidité. 
			\newline Détaillons maintenant la procédure qui permet de crée ses tunnels. Comme nous sommes en JAVA, une seule classe permet de crée un tunnel et cette classe est ensuite instanciée autant de fois que l'on veut.
			\newline Voici le code (Disponible dans /SSH/Exec.java) de création d'un tunnel :
			
			\begin{lstlisting}[language=java]
try{
	JSch jsch=new JSch();
	this.session=jsch.getSession("pi", "169.254.14.03", 22);
	UserInfo ui=new MyUserInfo();
  this.session.setUserInfo(ui);
  this.session.connect();
  this.channel = this.session.openChannel("exec");
  ((ChannelExec)this.channel).setCommand(this.Commande);
  this.channel.setInputStream(null);
  ((ChannelExec)this.channel).setErrStream(System.err);
  this.in=this.channel.getInputStream();
  this.channel.connect();
  byte[] tmp=new byte[1024];
  while(true){
		while(this.in.available()>0){
			int i=this.in.read(tmp, 0, 1024);
      if(i<0)break;
      System.out.print(new String(tmp, 0, i));
      this.retour=new String(tmp, 0, i);
    }
    if(channel.isClosed()){
			if(this.in.available()>0) continue; 
			System.out.println("exit-status: "+channel.getExitStatus());
      break;
     }
   }
}
catch(Exception e){
	System.out.println(e);
}
			\end{lstlisting}
			De la ligne 1 à 5, le tunnel est crée et les informations tel que le nom d'utilisateur, le mot de passe, l'adresse IP et le port sont ajouté aux couches correspondante du tunnel, puis ligne 6 la session est lancée.
		\newline A la ligne 7, nous ouvrons un canal d’exécution de commande et ligne 8 nous donnons à ce canal la commande que nous voulons envoyée.
		\newline Les lignes 9,10 et 11 définissent où vont les données entrées, sorties et sorties erreur. Dans notre cas l'entrée ne nous intéresse pas car cela passe par une commande, la sortie normal sera stockée et la sortie erreur renvoyée sur l'afficheur d'erreur du système (la console). La ligne 12 lance la connexion du canal, c'est ici que la commande est envoyée.
		\newline De la ligne 13 à 20 nous permet de récupérer les valeurs retournées par la Raspberry et de les stocker pour ensuite pouvoir les traiter.
		\newline Puis les dernières lignes, permettent de gérer le cas où le canal est coupé et nous renvoyer d'où vient l'erreur (par exceptions).
		\newline \newline Ces tunnels nous permettent d'envoyer des commandes à la Raspberry et de pouvoir récupérer le retour de cette commande. C'est par ce moyen que nous récupérons presque tous. L'exception étant pour la vidéo IP. Abordons ce sujet.
		\subsection{Vidéos}
		Nous avons donc 2 flux vidéos à récupérer depuis une adresse IP. Tout d'abord nous devons introduire quelque chose que nous utilisons partout dans notre code: le multi-Thread. Cela permet de lancer plusieurs actions en même temps, c'est ce qu'il se passe avec la récupération des flux vidéos. Chaque image des flux vidéos est récupérée, traitée puis affichée en temps réel sans interrompre le reste du programme, tout comme l'envoie de chaque commande.
		\newline Pour les flux vidéos, c'est une connexion http qui est effectuée, pour cela la méthode connect est appelée:
		\begin{lstlisting}[language=java]
public void connect()
	{
		try
		{
			URL u = new URL(useMJPGStream?mjpgURL:jpgURL);
			huc = (HttpURLConnection) u.openConnection();
			InputStream is = huc.getInputStream();
			connected = true;
			BufferedInputStream bis = new BufferedInputStream(is);
			dis= new DataInputStream(bis);
			if (!initCompleted) initDisplay();
		}
		catch(IOException e)
		{ //Relance la connexion si pas de connexion en attendant 60 sec
			try
			{
				huc.disconnect();
				Thread.sleep(60);
			}
			catch(InterruptedException ie)
			{
				System.out.println(ie);
			}
		}
		catch(Exception e){;}
	}
			\end{lstlisting}
			De la ligne 5 à 10, la procédure de connexion http est effectuée.
			\newline Après la ligne 12, on gère les exceptions liées à la connexion.
			\newline A la ligne 10, les données récupérées sont stockées dans une variable globale à Caméra.
			\newline Les informations vont être ensuite traité par initDisplay qui est appelée en ligne 11.
			\newline Observons cette méthode :
		\begin{lstlisting}[language=java]
public void initDisplay()
	{ 
		if (useMJPGStream)readMJPGStream();
		else
		{
			readJPG();
			disconnect();
		}
		imageSize = new Dimension((image.getWidth(this)*2), image.getHeight(this)*2);
		setPreferredSize(imageSize);
		parent.validate();
		initCompleted = true;
	}
		\end{lstlisting}
		Le premier If/Else permet de distinguer le cas où le flux serait une vidéo ou juste une photo. Dans notre cas c'est un flux vidéo composé d'image JPG.
		\newline Le reste de la méthode permet de préparer l'affichage des images.
		\newline Nous somme toujours dans la procédure de connexion, la lecture de la première image récupérée est faite. Pour cela la méthode readMJPGStream qui appel readJPG permet de décoder l'image et de la stocker dans la variable image. Voici les 2 méthodes :
		\begin{lstlisting}[language=java]
public void readMJPGStream()
	{
		readLine(4,dis); //enlève les 3 premières lignes
		readJPG();
		readLine(1,dis); //enlève les 2 dernières lignes
	}
	
public void readJPG()
	{
		try{
			JPEGImageDecoder decoder = JPEGCodec.createJPEGDecoder(dis);
			image = decoder.decodeAsBufferedImage();
		}catch(Exception e){
			disconnect();
		}
	}
		\end{lstlisting}
		La procédure de décodage d'une image JPEG est faite par une bibliothèque externe.
		\newpage Après cette procédure de connexion, les 2 méthodes ci dessus sont appelées en boucle et l'affichage mis à jour:
		\begin{lstlisting}[language=java]
public void readStream()
	{
		try{
			if (useMJPGStream){
				while(true){
					readMJPGStream();
					parent.repaint();
				}
			}
    	}catch(Exception e){;}
    }
		\end{lstlisting}
		L'affichage étant gérée par la bibliothèque Swing, c'est la méthode paint() qui affiche l'image et de plus trace une ligne qui en fonction des angles d’Euler renvoyés par la centrale inertielle :
		\begin{lstlisting}[language=java]
public void paint(Graphics g)
	{
		if (image != null)
			image=scale(image, 2);
			g.drawImage(image, 0, 0, this);
			Graphics2D g2 = (Graphics2D) g;
			double alpha = Interface.rotZ* Math.PI/180f;
    	int a = image.getHeight();
    	int b = image.getWidth();
    	double S =(b/2)*(Math.sin(alpha))*(Math.cos((Math.PI/2)-alpha));
    	double T =(b/2)*(Math.sin(alpha))*(Math.sin((Math.PI/2)-alpha));
    	g2.draw(new Line2D.Double(S,(a/2)-T,b-S,(a/2)+T));
	}
		\end{lstlisting}
	L'image est redimensionnée pour le bien de l'affichage et la ligne est tracé avec 2 points calculés par rapport à une rotation avec une origine au centre de l'image.
	\newline \newline Nos 2 flux vidéos sont donc récupérés et peuvent donc être appelés par un JPanel n'importe où.
\newpage
		\subsection{Capteurs et Moteurs}
		\subsubsection{Capteurs}
		Nous avons déjà précédemment préparé la Raspberry pour qu'elle renvoit les informations que l'on veut en fonction d'une commande. Il nous suffit maintenant d'envoyer en temps réel et en boucle infini les commandes (capteur de pression et centrale inertielle) grâce au système de multi-thread.
		\newline Expliquons la méthode pour le capteur de pression. Tout d'abord il faut crée le thread lié à la classe qui sera exécuté en boucle, puis on lance le thread avec la méthode, ce qui donne :
		\begin{lstlisting}[language=java]
Pression ex4 = new Pression();
Thread a4 = new Thread(ex4);
a4.start();
		\end{lstlisting}
		La classe Pression doit être héritière de Runnable pour permettre le lancement en thread.
		\newline Observons dans la classe Pression, la méthode start:
		\begin{lstlisting}[language=java]
Interface.exPression.Commander("python MS5803_14BA.py");
String[] a = Interface.exPression.retour.split("/");
this.Pression=a[0];
this.TemperatureC=a[1];
this.TemperatureF=a[2];
Interface.pre=Pression;
Interface.tempC=TemperatureC;
Interface.tempF=TemperatureF;
Interface.pression.setText(" Pression = "+Interface.pre);
Interface.pression.repaint();
Interface.temperatureC.setText(" TemperatureC = "+Interface.tempC);
Interface.temperatureC.repaint();
Interface.temperatureF.setText(" TemperatureF = "+Interface.tempF);
Interface.temperatureF.repaint();
		\end{lstlisting}
		Nous commençons en ligne 1 par envoyer la commande grâce au tunnel précédemment crée pour le capteur de Pression puis nous récupérons les valeurs sous forme de chaînes de caractères.
		\newline Enfin nous mettons à jour les valeurs globales et l’affichage.
		
		\subsubsection{Moteurs}
		Pour les moteurs, on envoie juste une commande à la Raspberry :
		\begin{lstlisting}[language=java]
Interface.exMoteur.setCommande("echo 0="+m1+" > /dev/servoblaster & echo 1="+m2+" > /dev/servoblaster & echo 2="+m3+" > /dev/servoblaster");
Thread a1 = new Thread(Interface.exMoteur);
a1.start();
while( a1.isAlive()) {}
Interface.m1=this.m1;
Interface.m2=this.m2;
Interface.m3=this.m3;
Interface.moteur1.setText(""+Interface.m1+"    ");
Interface.moteur1.repaint();
Interface.moteur2.setText(""+Interface.m2+"    ");
Interface.moteur2.repaint();
Interface.moteur3.setText(""+Interface.m3+"    ");
Interface.moteur3.repaint();
		\end{lstlisting}
		On oublie pas de mettre à jour au passage l'affichage.
		\newline Ce code est donc exécuté à chaque fois que l'on appuie sur une des touches de directions.
		\newline Nous avons défini les touches suivantes:
		\newline Monter/Descente : Z/S
		\newline Gauche/Droite : Flèche Gauche/Droite
		\newline Monter/Descente : Z/S
		\newline Arrête d'urgence : Barre Espace
		
		\subsection{Affichage 3D}
			\label{subsec:Affichage 3D}
			Nous utilisons JAVA3D pour afficher le modèle qui est extrait de Solidworks.
			\newline Tout d'abord nous devons crée un canvas 3D qui contiendra notre objet 3D et nous l’insérons au milieux d'un JPanel :
		\begin{lstlisting}[language=java]
Canvas3D canvas3D = new Canvas3D(SimpleUniverse.getPreferredConfiguration());
this.add(canvas3D, BorderLayout.CENTER);
		\end{lstlisting}
		Puis nous créons un simple univers qui contient notre canvas3D.
		\newline Nous devons maintenant positionner notre point d'observation pour avoir une vue correcte:
		\begin{lstlisting}[language=java]
OrbitBehavior orbit = new OrbitBehavior(canvas3D, OrbitBehavior.REVERSE_ROTATE);
orbit.setRotXFactor(0);//or any other value
orbit.setRotYFactor(0);
orbit.setTransXFactor(0);
orbit.setTransYFactor(0);
orbit.setSchedulingBounds(new BoundingSphere());
simpleU.getViewingPlatform().setViewPlatformBehavior(orbit);
ViewingPlatform vp = simpleU.getViewingPlatform();
TransformGroup steerTG = vp.getViewPlatformTransform();
Transform3D t3d = new Transform3D();
steerTG.getTransform(t3d);
t3d.lookAt(new Point3d(-1.2,1.2,1.2), new Point3d(0,0,0), new Vector3d(0,1,0));
t3d.invert();
steerTG.setTransform(t3d);
		\end{lstlisting}
		De la ligne 1 à 6, nous définissions un mouvement orbital de la caméra puis pour le moment nous fixons les rotations et les translations (on pourra les débloquer si on le veut)
		\newline Les lignes 9 à 14 permettent de définir la position initiale de notre point d'observation.
		\newline Nous devons ensuite crée ce qu'on appelle une scène, c'est dans cette scène que tous nos objets 3d se trouveront:
		\begin{lstlisting}[language=java]
BranchGroup scene = createSceneGraph(simpleU);
scene.compile();
simpleU.addBranchGraph(scene);
		\end{lstlisting}
		Les 2 ligns suivant compile la scène et rattache notre scène à l'univers.
		\newline \newline Maintenant nous devons crée cette scène 3d qui contiendra notre objet mais aussi la lumière, notre eau fictive et les mouvements possible.
		\newline Tous ce passe dans la méthode createSceneGraph.
		\begin{lstlisting}[language=java]
public BranchGroup createSceneGraph(SimpleUniverse simpleU) 
	{
    BranchGroup parent = new BranchGroup();
    BoundingSphere bounds = new BoundingSphere(new Point3d(), 100);
    Light ambientLight = new AmbientLight(new Color3f(Color.white));
    ambientLight.setInfluencingBounds(bounds);
    parent.addChild(ambientLight);
		
    Light directionalLight = new DirectionalLight(
      new Color3f(Color.white),
      new Vector3f(1, -1, -1));
    directionalLight.setInfluencingBounds(bounds);
    parent.addChild(directionalLight);
		\end{lstlisting}
		La ligne 3 crée un objet parent qui contiendra tous nos objets.
		\newline De la ligne à 4 à 7, on crée une lumière ambiante de couleur blanche
		\newline Puis de la ligne 9 à la ligne 13, une lumière directionnel pour augmenter la luminosité dans la même direction que notre point d'observation.
		\newline Nous ne détaillerons pas ici le code de la création de l'eau, le principe étant qu'on a crée 4 plans positionnés correctement autour du ROV et on lui applique une texture bleu (que l'on peut changer facilement). Et on oublie pas de l'ajouter à l'objet parent.
		\newline Maintenant autorisons les mouvements de la souris pour notre objet :
		\begin{lstlisting}[language=java]
TransformGroup mouseTransform = new TransformGroup();
mouseTransform.setCapability(TransformGroup.ALLOW_TRANSFORM_READ);
mouseTransform.setCapability(TransformGroup.ALLOW_TRANSFORM_WRITE);
mouseTransform.addChild(loadWavefrontObject());
		\end{lstlisting}
		Et en ligne 4 nous ajoutons notre ROV. La méthode loadWavefrontObject() permet de récupérer un objet 3D à partir d'un fichier .obj.
		\newline Pour la fin de cette méthode, les commentaires décrivent les opérations effectuées
		\begin{lstlisting}[language=java]
// Création de l'homethetie (homothetie)
Transform3D homothetie = new Transform3D();
homothetie.setScale(Interface.scale); 
    
// Création de la transformation (translation)
 Transform3D translation = new Transform3D();
translation.setTranslation(new Vector3f(0f, 0f, 0f));
translation.mul(homothetie);
    
// Création de la rotation X(rotation)
Transform3D rotationX = new Transform3D();
rotationX.rotX( Interface.rotX * Math.PI/180f);
rotationX.mul(translation);
    
// Création de la rotation Y(rotation)
Transform3D rotationY = new Transform3D();
rotationY.rotY( Interface.rotY * Math.PI/180f);
rotationY.mul(rotationX);
    
// Création de la rotation Z(rotation)
Transform3D rotationZ = new Transform3D();
rotationZ.rotZ( Interface.rotZ * Math.PI/180f);
rotationZ.mul(rotationY);
    
this.rotationGroup = new TransformGroup(rotationZ);

//Autorisation de modifier les transformations
rotationGroup.setCapability(TransformGroup.ALLOW_TRANSFORM_READ);
rotationGroup.setCapability(TransformGroup.ALLOW_TRANSFORM_WRITE);
    
// Ajout au graphe de la scène
rotationGroup.addChild(mouseTransform);
parent.addChild(rotationGroup);

return parent;
		\end{lstlisting}
		Notre scène renvoie donc tous les objets qu'on a crée précédemment.
		\newline \newline Maintenant nous voulons que notre ROV 3D soit capable de se mouvoir en fonction des angles d’Euler renvoyés et stockés dans notre interface.
		\newline Pour cela on a crée une méthode mouvement:
		\begin{lstlisting}[language=java]
public void mouvement(double rotX, double rotY, double rotZ, Vector3d trans, double scale)
		\end{lstlisting}
		Elle prend donc en argument, les 3 rotations, un vecteur des translations (sur tous les axes) et un paramètre multiplicateur d’échelle.
		\newline Cette méthode modifie la matrice 4*4 contenant la matrice de rotation, translation et de mise à l’échelle.
		\newline Puis effectue les transformations de cette matrice.
		
		\subsection{Cartographie}
			\label{subsec:Cartographie}
			Cette partie n'a pas été beaucoup développé mais un premier système a été crée mais pas intégré dans la dernière version de l'interface.
			\newline Grâce à l'appuie sur une touche, une photo de la camera du dessous est enregistrée dans un dossier. Voici le code qui permet d'enregistrer notre photo en jpg :
			\begin{lstlisting}[language=java]
BufferedImage img = new BufferedImage(axPanel.getWidth(), axPanel.getHeight(), BufferedImage.TYPE_INT_RGB);
axPanel.print(img.getGraphics());
try {
	ImageIO.write(img, "jpg", new File(nomPhoto+".jpg"));
}
catch (IOException e5) {
	e5.printStackTrace();
}
		\end{lstlisting}
			Le système n'est pas fini mais dans l'absolu chaque photo serai enregistrée avec un nom différent avec les données de localisation dans les méta-données de la photo.
			\newline Ensuite il y a un autre bouton (non affiché sur la dernière interface) qui ouvre une autre fenêtre avec toutes nos photos positionnées, en fonction des coordonnées GPS, sur une carte.
			\newline On peut cliquer sur chaque photo pour les agrandir dans une nouvelle fenêtre.
			\newline Tous les codes se trouvent dans le sous-dossier /Carto.
			
\chapter{Conclusion}

\bibliographystyle{unsrt} % Le style est mis entre accolades.

\bibliography{bibliographie} % mon fichier de base de données s'appelle bibli.bib

\listoffigures

\end{document}

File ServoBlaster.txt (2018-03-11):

# Installation et configuration de ServoBlaster (commande à rentrer sur le terminal Raspbian) 

sudo apt-get install git
git clone https://github.com/richardghirst/PiBits.git
cd PiBits/ServoBlaster/user
nano init-script
# Supprimer la valeur --idle-timeout=2000 des options par défaut
nano servod.c
# Modifier la ligne 960 pour avoir "else if (strstr(modelstr, "BCM2709") || strstr(modelstr, "BCM2835"))"
make
sudo make install

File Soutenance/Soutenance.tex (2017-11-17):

\documentclass[a4paper,11pt]{report}
 
% Import des extensions
\usepackage[T1]{fontenc}
\usepackage[utf8]{inputenc}
\usepackage[english]{babel}
\usepackage{graphicx}
\usepackage{color}
\usepackage{colortbl}
\usepackage{geometry}
\usepackage{hyperref}
\usepackage{fullpage}
\usepackage{eso-pic}
\geometry{hmargin=2.5cm,vmargin=3.5cm}

\newcommand{\blap}[1]{\vbox to 0pt{#1\vss}}
\newcommand\AtUpperLeftCorner[3]{%
\put(\LenToUnit{#1},\LenToUnit{\dimexpr\paperheight-#2}){\blap{#3}}%
}
\newcommand\AtTopCenterPage[2]{%
\put(\LenToUnit{.5\paperwidth},\LenToUnit{\dimexpr\paperheight-#1}){\blap{\hbox to 0pt{\hss#2\hss}}}%
}
\newcommand\AtUpperRightCorner[3]{%
\put(\LenToUnit{\dimexpr\paperwidth-#1},\LenToUnit{\dimexpr\paperheight-#2}){\blap{\llap{#3}}}%
}

\author{Dylan Bideau, Julien Turpin, Pierre Bogrand, Guillaume Vincenti}
\title{\huge{Nautilus - Summary}}

\begin{document}
\makeatletter
\begin{titlepage}

	\AddToShipoutPicture{
		\AtUpperLeftCorner{1.5cm}{1cm}{}
	}
	\begin{center}
		\vspace*{10cm}
		\textsc{\@title}
		\vspace*{0.5cm}
		\hrule
		\vspace*{0.5cm}
		\large{\@author}
	\end{center}
	\vspace*{9.2cm}
	\begin{center}
		\large{\@date}
	\end{center}
\end{titlepage}
\ClearShipoutPicture
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

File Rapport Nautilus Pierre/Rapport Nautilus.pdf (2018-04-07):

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


# Sommaire

1 Introduction | 2
2 Présentation du projet | 3
3 Cahier des charges | 4
4 Motorisation et énergie | 6
5 Références | 12

1

# Chapitre 1

# Introduction

Les fonds marins réunissent aujourd'hui de nombreux secteurs et enjeux, tant professionels que particuliers. On y retrouve entre autre l'exploration sous-marine, la surveillance et maintenance d'installations professionelles, ainsi que la cartographie des fonds marins. Tout ces domaines demandent le développement de solutions techniques plus rentables et pratiques qu'une intervention humaine. Notre projet propose ainsi un ROV (Remotely
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

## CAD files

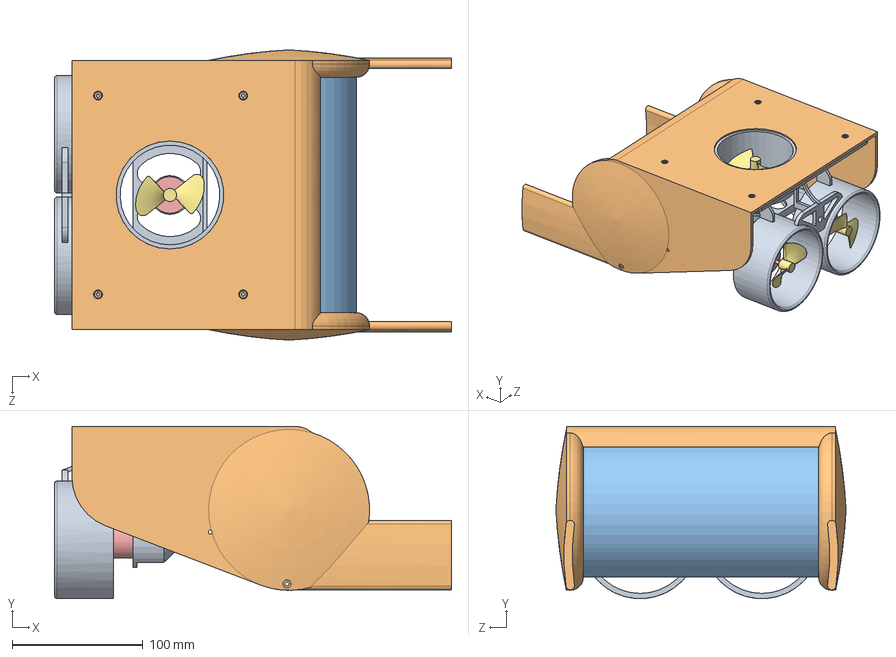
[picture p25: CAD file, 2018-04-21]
Solidworks/Assemblage1.SLDASM
303.6 x 131.8 x 222.0 mm
Interieur rov v2
coque
tube
bat
moteur x 3
poid x 2
Pièce3 x 3
Pièce4

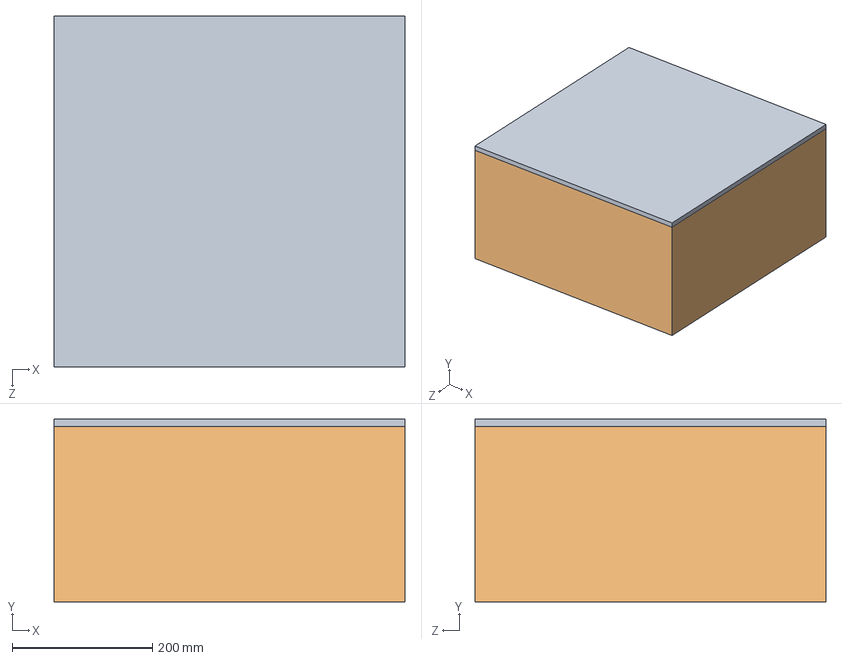
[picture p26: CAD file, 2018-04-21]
Solidworks/Assemblage2.SLDASM
500.0 x 260.0 x 500.0 mm
Interieur rov v2
coque
tube
bat
moteur x 3
poid x 2
Pièce3 x 3
Pièce4
Pièce1

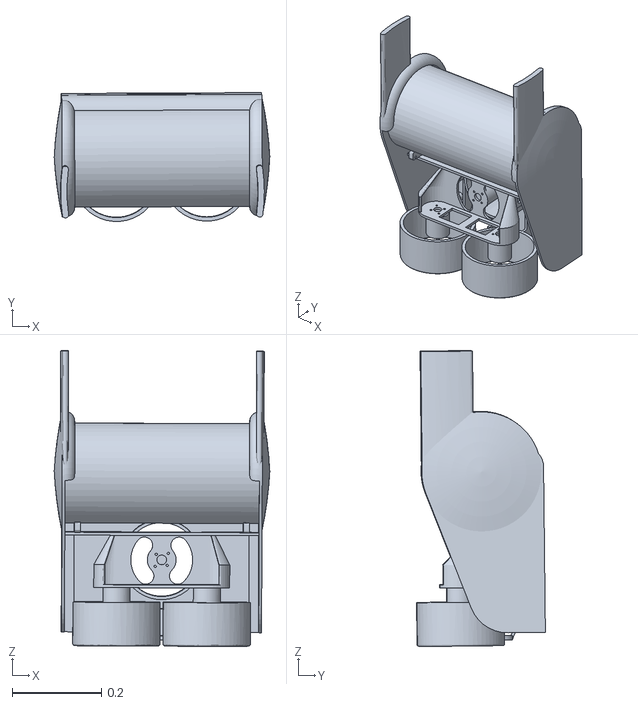
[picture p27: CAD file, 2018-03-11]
Interface/Nautilus/resources/singe.obj
0.484 x 0.289 x 0.665

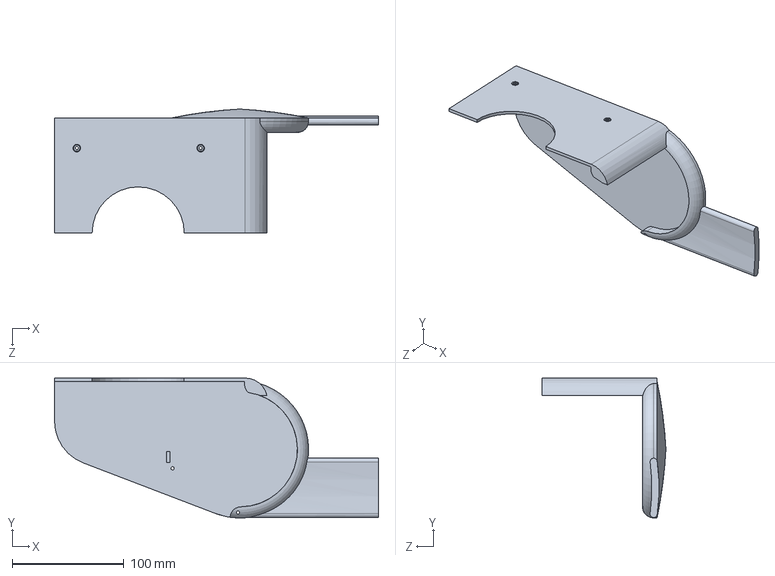
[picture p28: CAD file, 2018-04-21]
Solidworks/Corps4.sldprt
290.3 x 125.4 x 111.0 mm

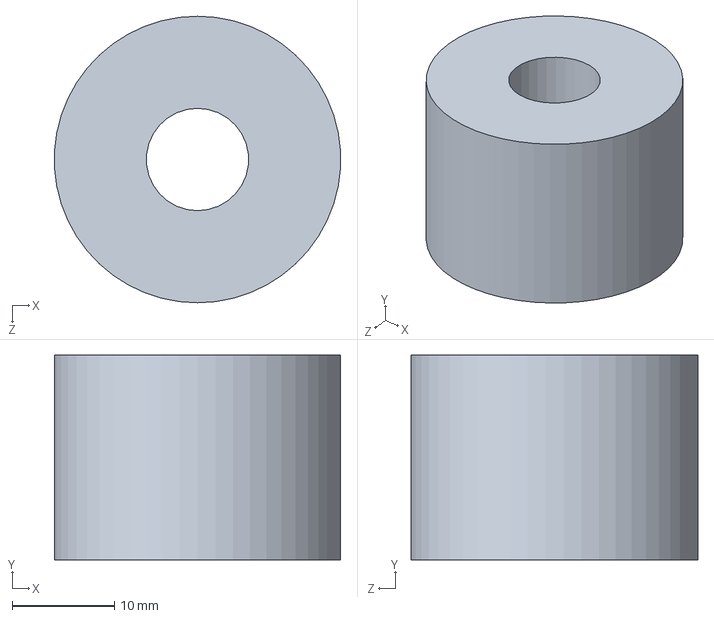
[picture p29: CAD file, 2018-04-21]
Solidworks/Pièce4.SLDPRT
27.9 x 20.0 x 28.0 mm

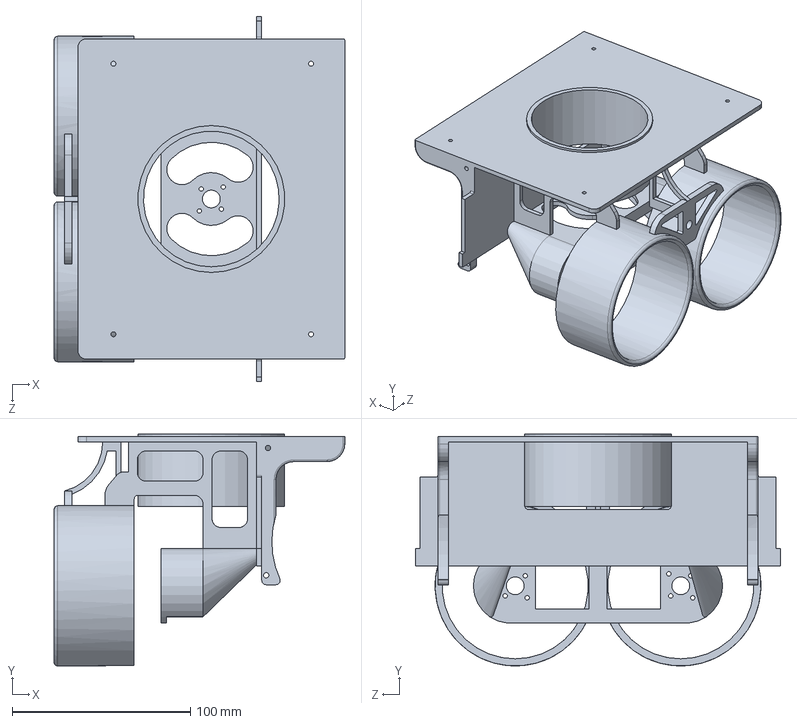
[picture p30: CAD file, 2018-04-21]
Solidworks/Interieur rov v2.SLDPRT
163.3 x 130.2 x 205.0 mm

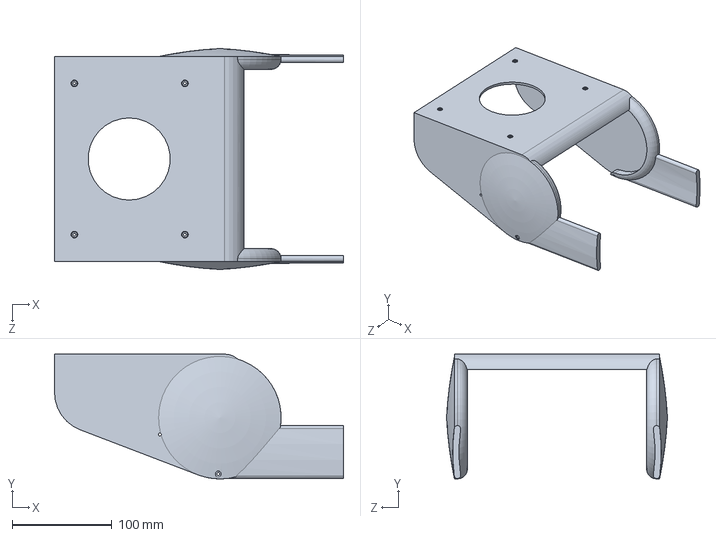
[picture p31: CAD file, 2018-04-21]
Solidworks/coque.SLDPRT
290.3 x 125.4 x 222.0 mm

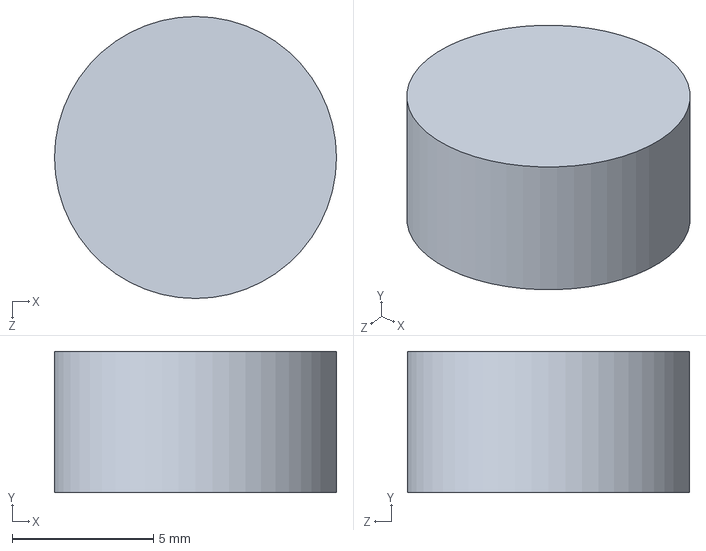
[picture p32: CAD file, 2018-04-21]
Solidworks/poid.SLDPRT
10.0 x 5.00 x 10.0 mm

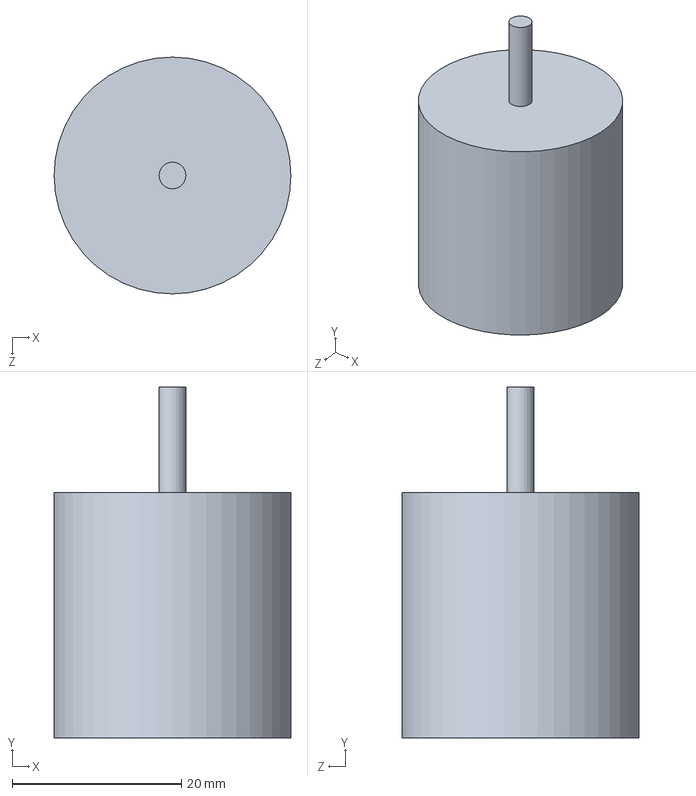
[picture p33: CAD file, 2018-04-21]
Solidworks/moteur.SLDPRT
28.0 x 41.5 x 28.0 mm

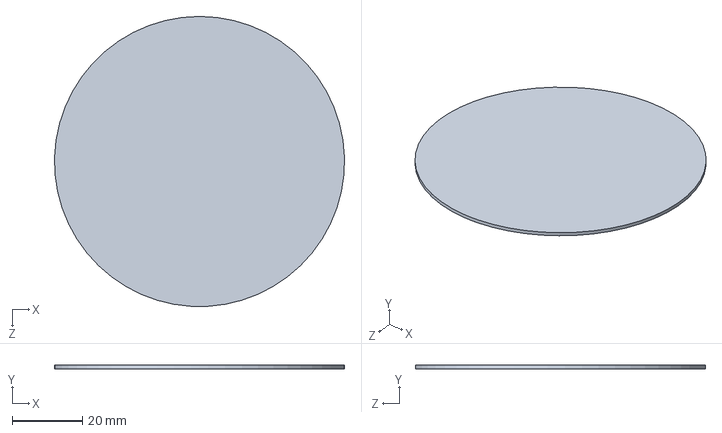
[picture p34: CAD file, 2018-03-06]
Solidworks/bouchon top.SLDPRT
82.5 x 1.00 x 82.5 mm

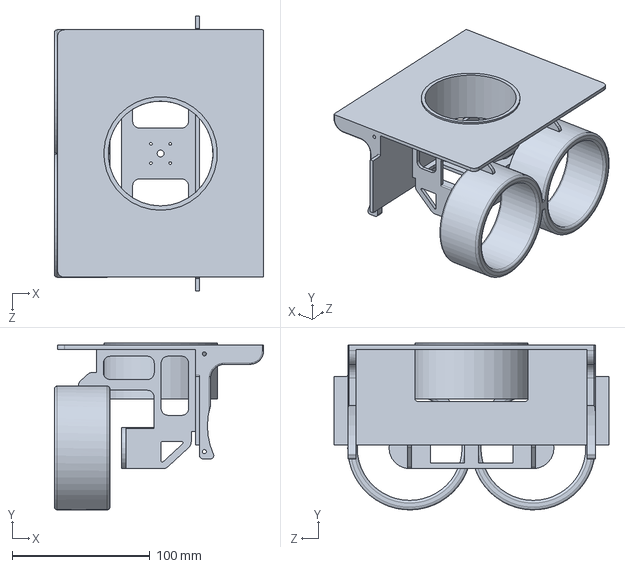
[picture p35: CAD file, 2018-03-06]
Solidworks/support moteur intérieur nautilus.SLDPRT
152.3 x 121.3 x 200.0 mm

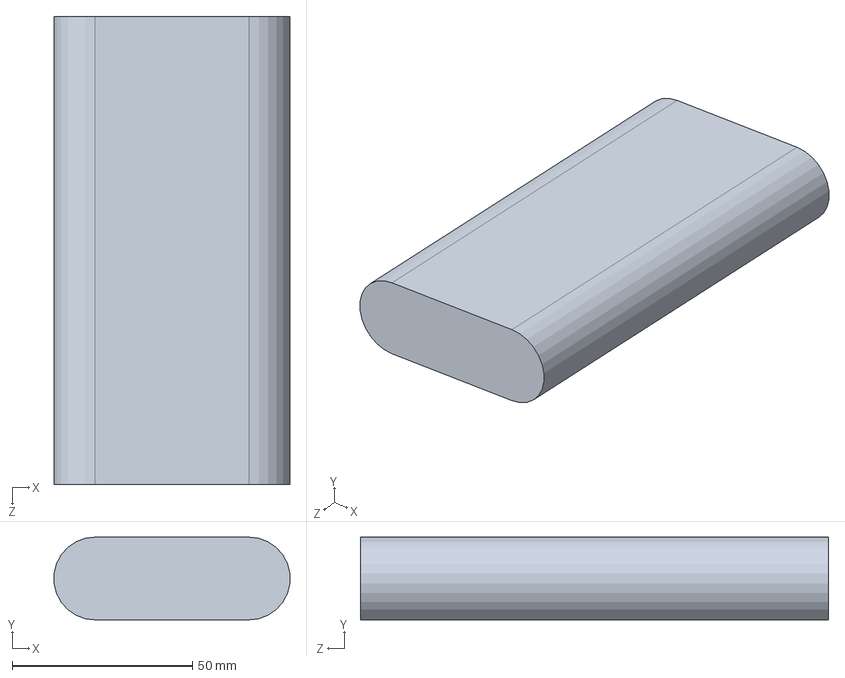
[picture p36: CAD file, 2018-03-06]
Solidworks/bat.SLDPRT
65.5 x 23.0 x 130.0 mm

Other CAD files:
Solidworks/Poulpi.SLDASM
Solidworks/coqueafract.SLDPRT
Solidworks/Corps2.sldprt
Solidworks/Corps3.sldprt
Solidworks/Corps1.sldprt
Solidworks/Corps3.STL
Solidworks/Corps4.STL
Solidworks/Interieur rov v2.STL
Solidworks/Pièce1.SLDPRT
Solidworks/Pièce2.SLDPRT
Solidworks/Pièce3.SLDPRT
Solidworks/Poulpi - Interieur rov v2-1.STL
Solidworks/Poulpi - Pièce3-1.STL
Solidworks/Poulpi - Pièce3-2.STL
Solidworks/Poulpi - Pièce3-3.STL
Solidworks/Poulpi - coque-1.STL
Solidworks/Poulpi - moteur-1.STL
Solidworks/Poulpi - moteur-2.STL
Solidworks/Poulpi - moteur-3.STL
Solidworks/Poulpi - poid-1.STL
Solidworks/Poulpi - poid-2.STL
Solidworks/Poulpi - tube-1.STL
Solidworks/Poulpi.3MF
Solidworks/Poulpi.AMF
Solidworks/Poulpi.STL
Solidworks/bouchon moteur.SLDPRT
Solidworks/coque v2.STL
Solidworks/coque.STL
Solidworks/makeProjectedPlanarWire.x_t
Solidworks/suppot moteur.SLDPRT
Solidworks/tube.SLDPRT

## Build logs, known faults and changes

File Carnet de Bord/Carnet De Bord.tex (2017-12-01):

\documentclass[a4paper,11pt]{report}
 
% Import des extensions
\usepackage[T1]{fontenc}
\usepackage[utf8]{inputenc}
\usepackage[francais]{babel}
\usepackage{graphicx}
\usepackage{color}
\usepackage{colortbl}
\usepackage{geometry}
\usepackage{hyperref}
\usepackage{fullpage}
\usepackage{eso-pic}
\geometry{hmargin=2.5cm,vmargin=3.5cm}

\newcommand{\blap}[1]{\vbox to 0pt{#1\vss}}
\newcommand\AtUpperLeftCorner[3]{%
\put(\LenToUnit{#1},\LenToUnit{\dimexpr\paperheight-#2}){\blap{#3}}%
}
\newcommand\AtTopCenterPage[2]{%
\put(\LenToUnit{.5\paperwidth},\LenToUnit{\dimexpr\paperheight-#1}){\blap{\hbox to 0pt{\hss#2\hss}}}%
}
\newcommand\AtUpperRightCorner[3]{%
\put(\LenToUnit{\dimexpr\paperwidth-#1},\LenToUnit{\dimexpr\paperheight-#2}){\blap{\llap{#3}}}%
}

\author{Dylan Bideau, Julien Turpin, Pierre Bogrand, Guillaume Vincenti}
\title{\huge{Nautilus - Carnet de Bord}}

\begin{document}
\makeatletter
\begin{titlepage}

	\AddToShipoutPicture{
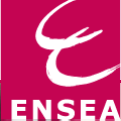
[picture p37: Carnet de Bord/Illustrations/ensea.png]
		\AtUpperLeftCorner{1.5cm}{1cm}{}
	}
	\begin{center}
		\vspace*{10cm}
		\textsc{\@title}
		\vspace*{0.5cm}
		\hrule
		\vspace*{0.5cm}
		\large{\@author}
	\end{center}
	\vspace*{9.2cm}
	\begin{center}
		\large{\@date}
	\end{center}
\end{titlepage}
\ClearShipoutPicture

\renewcommand{\contentsname}{Sommaire}
\tableofcontents

\chapter{Dylan Bideau}
	\section{Configuration Raspberry}
		\subsection{Raspbian}
			Tout d'abord il a fallu installer \underline{Raspbian} sur nos Raspberry Pi. \newline
			Nous l'avons téléchargé ici :\newline
			\url{https://www.raspberrypi.org/downloads/raspbian/}
			\newline Puis grâce à \underline{Win32DiskImager}, nous l'avons installé sur la carte. Ensuite il a fallu trouver un clavier, une souris et un ecran pour pouvoir acceder à notre Raspberry. Pour nos besoin futur il nous faut fixer l'adresse IP de la carte en modifiant \underline{cmdline.txt} sur la base de la microSD de la Raspberry. Nous avons choisit de commencer toutes les notre par 169.254.14. puis 01 pour Julien, 02 pour Pierre et Guillaume et 03 pour Dylan.
			
		\subsection{VNC server}
			\subsubsection{Partie Raspberry}
			Dans un second temps, nous avons voulu interagir avec la Raspberry sans avoir à utiliser un nouvel ecran, 			souris, clavier. Pour cela, nous utilisons VNC pour se connecter à distance avec un cable ethernet. \newline
			Voici le tutoriel dont nous nous sommes inspiré :\newline
			\url{http://www.framboise314.fr/prenez-vraiment-la-main-a-distance-sur-votre-raspberry-pi-avec-x11vnc/}
			\newline Tout d'abord, il faut mettre à jour le systeme :
			\begin{figure}[!h]
				\begin{center}
					
				\end{center}
			\end{figure}
			\newline Puis nous installons VNC sur notre carte :
			\begin{figure}[!h]
				\begin{center}
					
				\end{center}
			\end{figure}
			\newpage L'installation fini, il faut aller dans le menu pour configurer VNC server :
			\begin{figure}[!h]
				\begin{center}
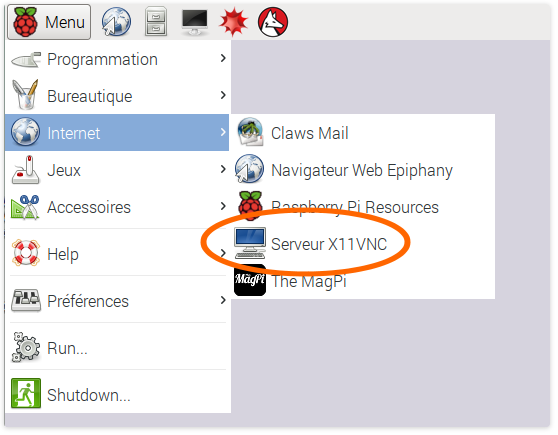
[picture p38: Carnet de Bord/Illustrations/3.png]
					
				\end{center}
			\end{figure}
			\newline Nous allons utilisé le port 5900 pour notre connection à distance
			\begin{figure}[!h]
				\begin{center}
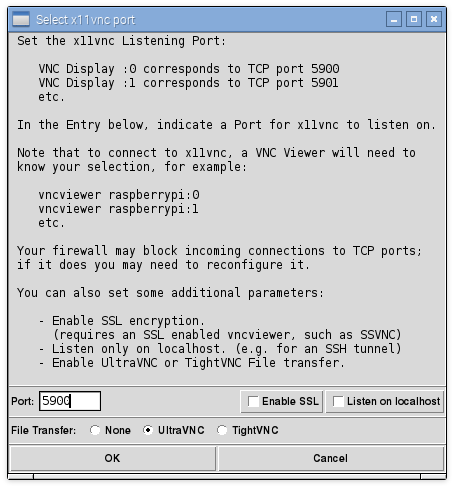
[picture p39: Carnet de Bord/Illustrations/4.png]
					
				\end{center}
			\end{figure}
			\newline Après avoir appuyé sur OK, nous cochons 3 cases qui nous permettront de nous connecter à distance :
			\begin{figure}[!h]
				\begin{center}
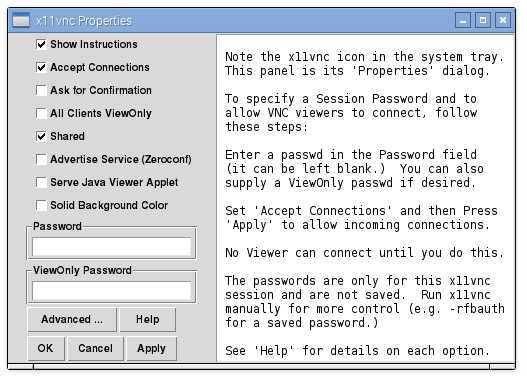
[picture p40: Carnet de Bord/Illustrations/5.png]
					
				\end{center}
			\end{figure}
			\newline En tant que password, nous avons laisser "raspberry" le code de base de la carte. Le serveur est donc lançé en manuelle.
			\newline \newline Maintenant il nous faut demarrer automatiquement le serveur VNC à chaque demarrage pour ne pas avoir à le lancer manuellement à chaque lancement. Nous allons pour cela crée un fichier mot de passe :
			\begin{figure}[!h]
				\begin{center}
					
				\end{center}
			\end{figure}
			\newline Pour finir il faut crée le service qui va se lancer à chaque demarrage :
			\begin{figure}[!h]
				\begin{center}
					
				\end{center}
			\end{figure}
			\newline Et y ecrire cela :
			\begin{figure}[!h]
				\begin{center}
					
				\end{center}
			\end{figure}
			\newline Il reste plus qu'à demander au systeme de le prendre en compte :
			\begin{figure}[!h]
				\begin{center}
					
				\end{center}
			\end{figure}
			\newline Maintenant passons à la partie PC \newpage
			
			\subsubsection{Partie PC}
			Il suffit d'installer VNC viewer sur nos PC, qui se trouve ici :
			\url{https://www.realvnc.com/en/connect/download/viewer/}
			\newline en voici le resultat :
			\begin{figure}[!h]
				\begin{center}
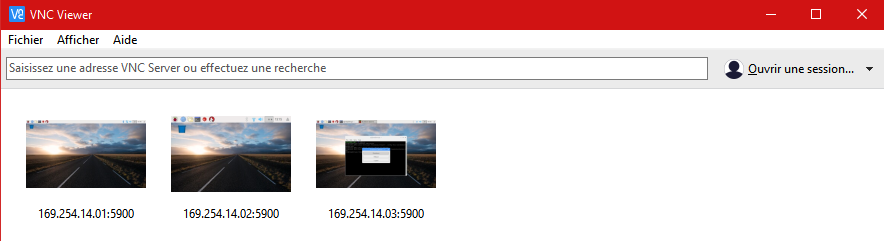
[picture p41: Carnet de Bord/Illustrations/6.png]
					
				\end{center}
			\end{figure}
			
		\subsection{Les Cameras}
		
		\subsubsection{Camera V2}
		
			Tout d'abord il faut brancher la camera au port prévu sur la raspberry. \newline
			Puis nous devons activer la camera dans les configurations de la rapsberry :
			\begin{figure}[!h]
				\begin{center}
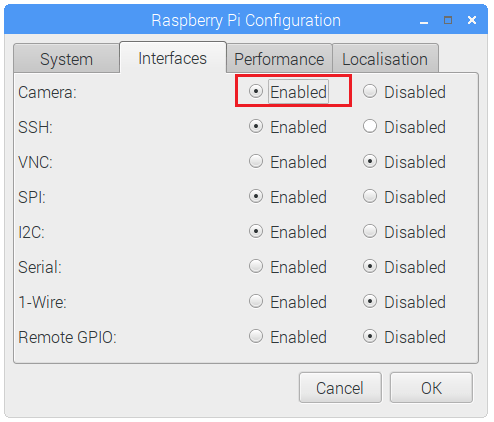
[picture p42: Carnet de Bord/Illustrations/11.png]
					
				\end{center}
			\end{figure}
		  \newline Nous créeons ensuite le script Python qui va permettre d'envoyer le flux video en streaming sur une IP (169.254.14.0X:8000)
			\begin{figure}[!h]
				\begin{center}
					
				\end{center}
			\end{figure}
			\newline Le code est stocké sur notre gitHub.\newpage
			Puis nous demarrons notre flux IP par cette commande :
			\begin{figure}[!h]
				\begin{center}
					
				\end{center}
			\end{figure}
			
			\subsubsection{Camera C170 Logitech}
			
			Nous installons Motion, un systeme qui permet de gerer une camera exterieur de façon très personnalisée \newline Tout d'abord installons le :
			\begin{figure}[!h]
				\begin{center}
					
				\end{center}
			\end{figure}
			\newline On va créer un dossier dans lequel les informations et instantanés seront archivées :
			\begin{figure}[!h]
				\begin{center}
					
				\end{center}
			\end{figure}
			\newline On va s’intéresser maintenant au fichier de configuration :
			\begin{figure}[!h]
				\begin{center}
					
				\end{center}
			\end{figure}
			\newline Le fichier de configuration est sur github.
			\newline Le daemon (service) motion est désactivé par défaut, pour l'autoriser:
			\begin{figure}[!h]
				\begin{center}
					
				\end{center}
			\end{figure}
			
			\chapter{Julien Turpin}

\chapter{Pierre et Guillaume}

\end{document}

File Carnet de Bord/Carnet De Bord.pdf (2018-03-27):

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

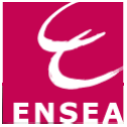
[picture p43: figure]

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

# Chapitre 1

# Dylan Bideau

1.1 | Conguration Raspberry
1.1.1 | Raspbian

Tout d'abord il a fallu installer Raspbian sur nos Raspberry Pi.
Nous l'avons téléchargé ici :
https://www.raspberrypi.org/downloads/raspbian/
Puis grâce à Win32DiskImager, nous l'avons installé sur la carte. Ensuite il a fallu trouver un clavier, une souris et un ecran pour pouvoir acceder à notre Raspberry. Pour nos besoin futur il nous faut xer l'adresse IP de la carte en modiant cmdline.txt sur la base de la microSD de la Raspberry. Nous avons choisit de commencer toutes les notre par 169.254.14. puis 01 pour Julien, 02 pour Pierre et Guillaume et 03 pour Dylan.

1.1.2 VNC server

Partie Raspberry

Dans un second temps, nous avons voulu interagir avec la Raspberry sans avoir à utiliser un nouvel ecran, souris, clavier. Pour cela, nous utilisons VNC pour se connecter à distance avec un
cable ethernet.
Voici le tutoriel dont nous nous sommes inspiré : http://www.framboise314.fr/prenez-vraiment-la-main-a-distance-sur-votre-raspberry-pi-avec-x11vnc/ Tout d'abord, il faut mettre à jour le systeme :

Puis nous installons VNC sur notre carte :

2

L'installation ni, il faut aller dans le menu pour congurer VNC server :

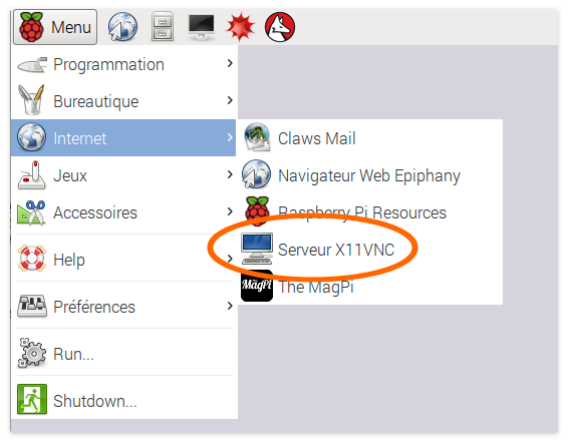
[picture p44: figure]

Nous allons utilisé le port 5900 pour notre connection à distance


Après avoir appuyé sur OK, nous cochons 3 cases qui nous permettront de nous connecter à distance :


3

En tant que password, nous avons laisser "raspberry" le code de base de la carte. Le serveur est donc lançé en manuelle.

Maintenant il nous faut demarrer automatiquement le serveur VNC à chaque demarrage pour ne pas avoir à le lancer manuellement à chaque lancement. Nous allons pour cela crée un chier mot de passe :

Pour nir il faut crée le service qui va se lancer à chaque demarrage :

Et y ecrire cela :

Il reste plus qu'à demander au systeme de le prendre en compte :

Maintenant passons à la partie PC

4

Partie PC

Il sut d'installer VNC viewer sur nos PC, qui se trouve ici : https://www.realvnc.com/en/connect/download/viewer/ (https://www.realvnc.com/en/connect/download/viewer/)
en voici le resultat :

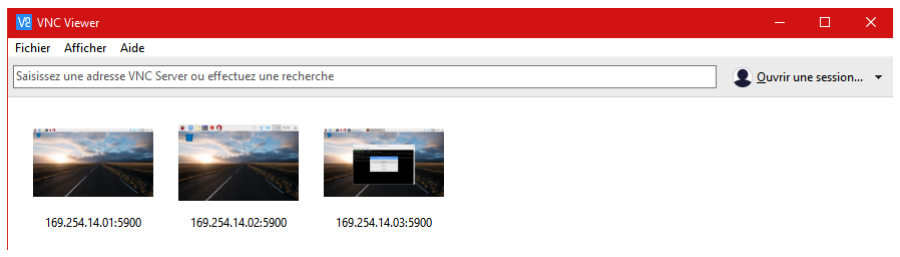
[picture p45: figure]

1.1.3 Les Cameras

Camera V2

Tout d'abord il faut brancher la camera au port prévu sur la raspberry. Puis nous devons activer la camera dans les congurations de la rapsberry :


Nous créeons ensuite le script Python qui va permettre d'envoyer le ux video en streaming sur une IP (169.254.14.0X :8000)

Le code est stocké sur notre gitHub.

5

Puis nous demarrons notre ux IP par cette commande :

Camera C170 Logitech

Nous installons Motion, un systeme qui permet de gerer une camera exterieur de façon très personnalisée
Tout d'abord installons le :

On va créer un dossier dans lequel les informations et instantanés seront archivées :

On va s'intéresser maintenant au chier de conguration :

Le chier de conguration est sur github.
Le daemon (service) motion est désactivé par défaut, pour l'autoriser :

6

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

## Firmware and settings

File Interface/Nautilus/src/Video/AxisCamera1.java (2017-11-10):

package Video;

import java.net.*;
import com.sun.image.codec.jpeg.*;
import java.io.*;
import java.awt.*;
import java.awt.image.*;
import javax.swing.*;
 
 
public class AxisCamera1 extends JPanel implements Runnable
{
    public boolean useMJPGStream = true; //still image set to false
    //streaming set to true
    public String jpgURL="http://169.254.14.03:8081/";
    //public String mjpgURL="http://169.254.14.03:8000/stream.mjpg";
    public String mjpgURL="http://169.254.14.03:8081/";
    DataInputStream dis;
    private BufferedImage image=null;
    int counter=0;
 
    public Dimension imageSize = null;
    public boolean connected = false;
    private boolean initCompleted = false;
    HttpURLConnection huc=null;
    Component parent;
 
    /** Creates a new instance of AxisCamera1 */
    public AxisCamera1(Component parent_) {
    parent = parent_;
    }
 
    public static Image getScaledInstanceAWT(BufferedImage source, double factor) {
    int w = (int) (source.getWidth() * factor);
    int h = (int) (source.getHeight() * factor);
    return source.getScaledInstance(w, h, Image.SCALE_SMOOTH);
    }
 
    public static BufferedImage toBufferedImage(Image image) {
    new ImageIcon(image); //load image
    int w = image.getWidth(null);
    int h = image.getHeight(null);
    BufferedImage bimage = new BufferedImage(w, h, BufferedImage.TYPE_BYTE_INDEXED);
    //BufferedImage bimage = getDefaultConfiguration().createCompatibleImage(w, h, Transparency.OPAQUE);
    Graphics2D g = bimage.createGraphics();
    g.drawImage(image, 0, 0, null);
    g.dispose();
    return bimage;
    }
 
    public void connect()
    {
        try
        {
            URL u = new URL(useMJPGStream?mjpgURL:jpgURL);
            huc = (HttpURLConnection) u.openConnection();
            //System.out.println("huc="+huc);
            System.out.println(huc.getInputStream());
            InputStream is = huc.getInputStream();
            //System.out.println("is="+is);
            connected = true;
            BufferedInputStream bis = new BufferedInputStream(is);
            //System.out.println("bis="+bis);
            dis= new DataInputStream(bis);
            if (!initCompleted) initDisplay();
        }
        catch(IOException e)
        { //incase no connection exists wait and try again, instead of printing the error
 
            try
            {
                huc.disconnect();
                Thread.sleep(60);
            }
            catch(InterruptedException ie)
            {
                //huc.disconnect();connect();
            }
            //connect();
        }
        catch(Exception e){;}
    }
 
    public void initDisplay()
    { //setup the display
        if (useMJPGStream)readMJPGStream();
        else
        {
            readJPG();
            disconnect();
        }
        imageSize = new Dimension(image.getWidth(this), image.getHeight(this));
        setPreferredSize(imageSize);
        parent.setSize(imageSize);
        parent.validate();
        initCompleted = true;
    }
 
    public void disconnect(){
    	try{
    		if(connected){
    			dis.close();
    			connected = false;
    		}
    	}catch(Exception e){;}
    }
 
    public void paint(Graphics g) { //used to set the image on the panel
    	if (image != null)
    		g.drawImage(image, 0, 0, this);
    }
 
    public void readStream(){ //the basic method to continuously read the stream
    	try{
    		if (useMJPGStream){
    			while(true){
    				readMJPGStream();
    				parent.repaint();
    			}
    		}
    		else{
    			while(true){
    				connect();
    				readJPG();
    				parent.repaint();
    				disconnect();
    				
    			}
    		}
 
    	}catch(Exception e){;}
    }
 
 
    public void readMJPGStream(){ //preprocess the mjpg stream to remove the mjpg encapsulation
    	readLine(4,dis); //discard the first 3 lines
    	readJPG();
    	readLine(1,dis); //discard the last two lines
    }
 
    public void readJPG(){ //read the embedded jpeg image
    	try{
    		JPEGImageDecoder decoder = JPEGCodec.createJPEGDecoder(dis);
    		image = decoder.decodeAsBufferedImage();
 
    		String s="a"+counter+".jpg";
    		counter++;
    		String filename="c://find_stillset/"+s;
    		//System.out.println(filename);
 
    		BufferedImage smaller = toBufferedImage(getScaledInstanceAWT(image, 1.0/3.0));//scalling image size
 
    		try {
    			OutputStream out = new FileOutputStream(filename);
    			JPEGImageEncoder encoder = JPEGCodec.createJPEGEncoder(out);
    			encoder.encode(smaller);
    			out.close();
    		} catch (Exception e) {
    			System.out.println(e);
    		}
 
    	}catch(Exception e){e.printStackTrace();disconnect();}
    }
 
    public void readLine(int n, DataInputStream dis){ //used to strip out the header lines
    	for (int i=0; i<n;i++){
    		readLine(dis);
    	}
    }
 
    public void readLine(DataInputStream dis){
    	try{
    		boolean end = false;
    		String lineEnd = "\n"; //assumes that the end of the line is marked with this
    		byte[] lineEndBytes = lineEnd.getBytes();
    		byte[] byteBuf = new byte[lineEndBytes.length];
    		
    		while(!end){
    			dis.read(byteBuf,0,lineEndBytes.length);
    			String t = new String(byteBuf);
    			//System.out.print(t); //uncomment if you want to see what the lines actually look like
    			if(t.equals(lineEnd)) end=true;
    		}
    	}catch(Exception e){e.printStackTrace();}
 
 
    }
    public void run() {
        System.out.println("in Run...................");
        connect();
        readStream();
    }
 
    public static void main(String[] args) {
 
        //System.setProperty("http.proxyHost","proxy.tp.edu.sg");
    	//System.setProperty("http.proxyPort","80");
    	JFrame jframe = new JFrame();
    	jframe.setDefaultCloseOperation(JFrame.EXIT_ON_CLOSE);
    	AxisCamera1 axPanel = new AxisCamera1(jframe);
    	new Thread(axPanel).start();
    	jframe.getContentPane().add(axPanel);
    	jframe.pack();
    	jframe.show();
    }
 
}

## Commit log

2017-10-03 Ajout du cahier des charges
    Première version 03/10
2017-10-10 Fin du cahier des charges
2017-11-10 Carnet de Bord
    Premier commit
2017-12-01 Last Commit 01/12
    - Premiere Interface por la cartographie
    - Carnet de Bord continué
2018-01-16 Last Commit 16/01/18
    - Changement de PC
    - Changement de version eclipse : Oxygen v2
    - Librairie jsch intégrée
2018-02-08 Last Commit 08/02/18
    - Nouvelle Interface Graphique
    - Capteur de pression et température ajouté
2018-02-13 Last Commit 13/02/18
    - Interface amélioré
    - Temps de reponse amélioré
    - Commandes moteurs effectives
    [singe.obj]
2018-03-06 Le ROV superbement réalisé par seigneur Julien
    [Interieur rov v2.SLDPRT, Interieur rov v2.STL, NOV3608 - Novak Ballistic Racing Brushless Motor (8.5T).sldprt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]
2018-03-06 Installation et configuration de ServoBlaster
2018-03-11 Last Commit 11/03/18
    - menage
    - Ancien projet
    [singe.obj]
2018-03-11 Last Commit 11/03/18
    [singe.obj]
2018-04-21 Auto stash before merge of "master" and "origin/master"
    [Assemblage1.SLDASM, Assemblage2.SLDASM, Corps1.sldprt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]
2018-04-21 Last Commit 21/04/18 3
    - MAJ rapport
    - Rangement
    [Interieur rov v2.SLDPRT, Interieur rov v2.STL, NOV3608 - Novak Ballistic Racing Brushless Motor (8.5T).sldprt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]
